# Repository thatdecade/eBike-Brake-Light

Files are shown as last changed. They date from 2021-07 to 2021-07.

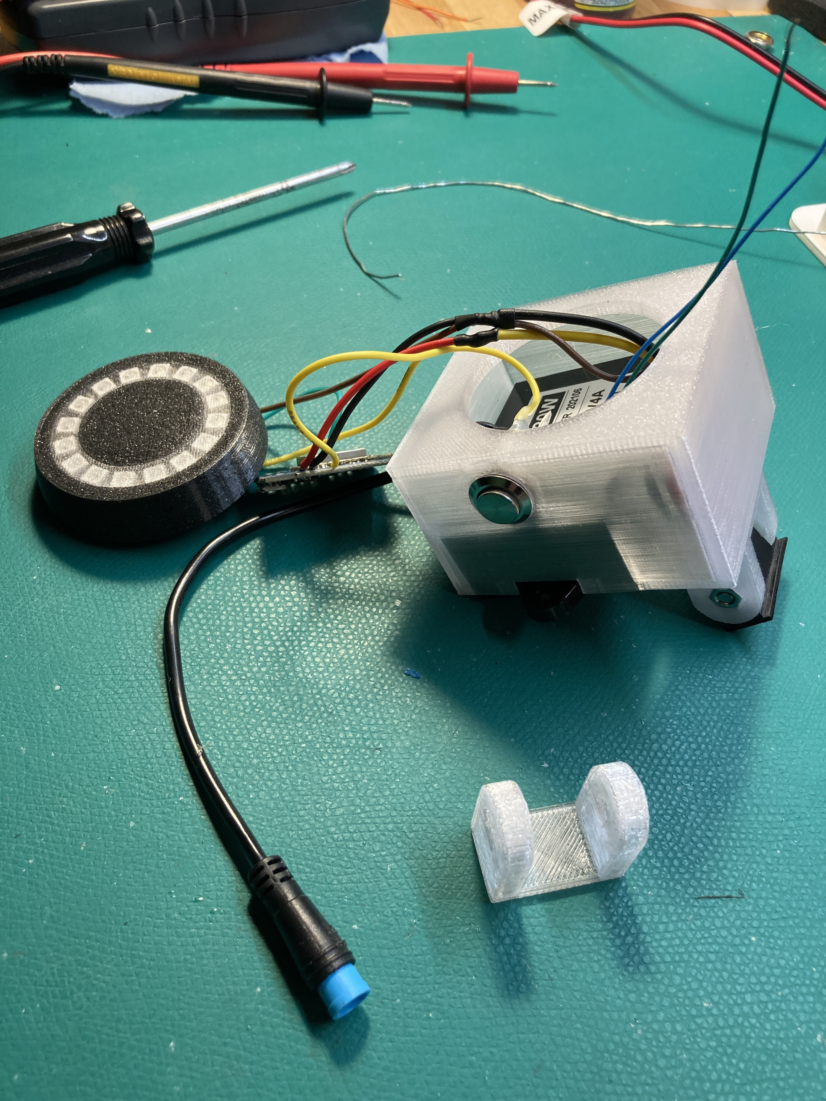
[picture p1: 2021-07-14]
photos/IMG_1149.jpg

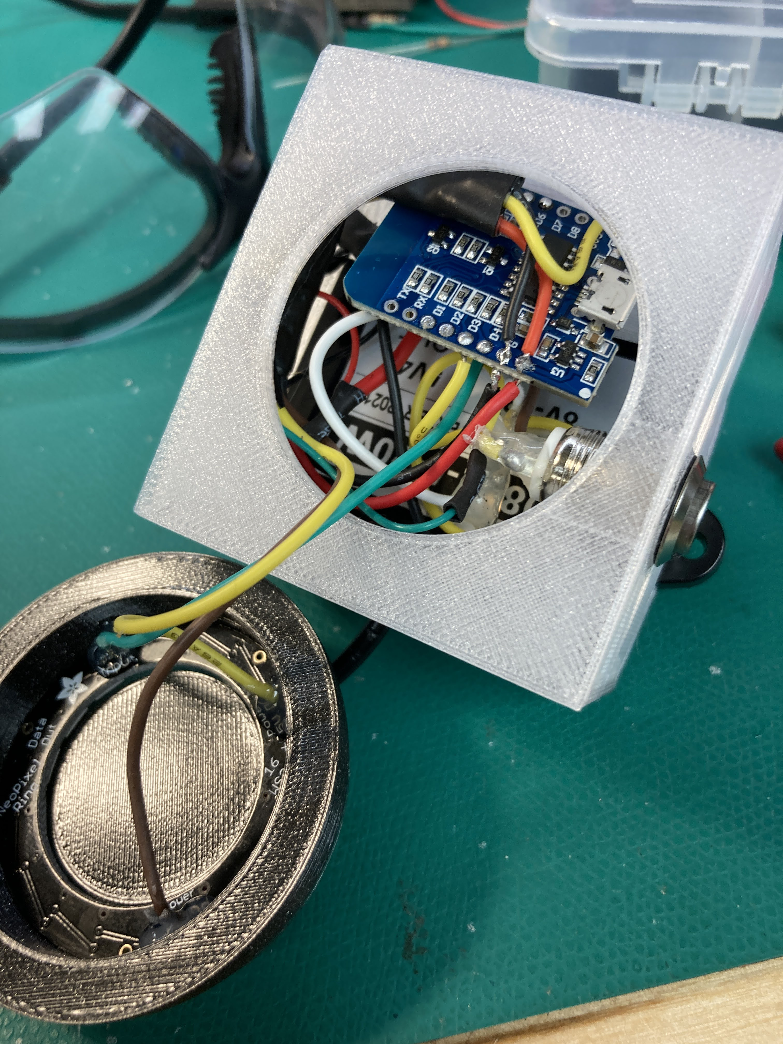
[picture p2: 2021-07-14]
photos/IMG_1154.jpg

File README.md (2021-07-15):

# eBike-Brake-Light
Neopixel Ring Based Brake Light

This is a brake light I made for my RadPower ebike.  Connects to the 4 pin wire harness from the motor controller.

The mount was modeled to replace my old Meilan light (https://amzn.to/3edWSh7) and re-use the same attachment bolt.  The openscad file is included, so you can change the mount to fit your project.



We are a participant in the Amazon Services LLC Associates Program, an affiliate advertising program designed to provide a means for us to earn fees by linking to Amazon.com and affiliated sites.

# Part List:

* Bafang 4 pin extension cable https://amzn.to/36BLSG1
* 8-72V to 5V 4A DCDC Converter https://amzn.to/3i4d8lV
* Wemos Mini dev board https://amzn.to/3xJ0e3q
* Adafruit neopixel Ring 16 https://amzn.to/3hDBBj0
* Pushbutton https://amzn.to/3egmDxg
* Resistors (5M / 10M) for voltage divider

# Wiring:

* 4 pin cable Red Wire -> DCDC +V Input
* 4 pin cable Black Wire -> DCDC GND Input
* 4 pin cable Green Wire -> +4.8V Voltage Divider
* 4 pin cable Blue Wire -> NO CONNECTION

* Wemos Pin 5V -> DCDC +V Output -> Neopixel V+
* Wemos Pin GND -> DCDC GND Output -> Neopixel GND -> Button GND

* Wemos Pin D3 -> Button
* Wemos Pin A0 -> 3.2V Brake Signal
* Wemos Pin D5 -> Neopixel Data In

# Cable Harness Wiring Notes:

The motor controller's 4 pin wire harness has two +52V and two grounds.  The voltages from the red and green wires are not meant to be combined, they do not have a common ground.  The red/black wire is supposed to power your 52V running lights, and the green/blue wire is supposed to power your 52V brake light.  I want all these signals running to a single circuit.

Here are some of the voltages I measured:

|Wire Pair|Lights Off|Lights On|Brake|Notes|
| --- | --- |  --- |  --- |  --- |
|Red / Black| 0| 52| 52| Correct ground|
|Green / Black| 4.8| 0| 4.8|Wrong ground|
|Blue / Black| 52| 52| 52|Wrong ground|
|Green / Blue| 0| 52| 0|Correct ground|
|Red / Blue| 52| 1.42| 1.55|Wrong ground|
|Red / Green| 4.8| 52| 52|Wrong ground|

**Correct ground**: These wires can sink current.
**Wrong ground**: Voltage drops to 0V if used for more than a few microamps.

There are a couple of ways to solve this.  
1. An optical isolator would be best.  Allowing the green/blue 52V brake signal to light up an LED, which then triggers a phototransistor to send a signal to our second 52V circuit.
2. Less good would be to try an read one circuit from the other using resistors and mixing the grounds.

I went with the second method.  The resistors are in the megaohm range, so less than 1uA is drawn from the green wires. The voltage does not drop and I can read it with an analog input set to detect a 0.2V threshold.

```

Green +4.8V ------- /\/\5M/\/\-+
                               |
                               +------ 3.2V to A0
                               |
Black GND   ------ /\/\10M/\/\-+

```

The wemos A0 pin has an additional voltage divider so the resulting signal is below 1V.  Measured 0.4V (idle) / 0.01V (brake)

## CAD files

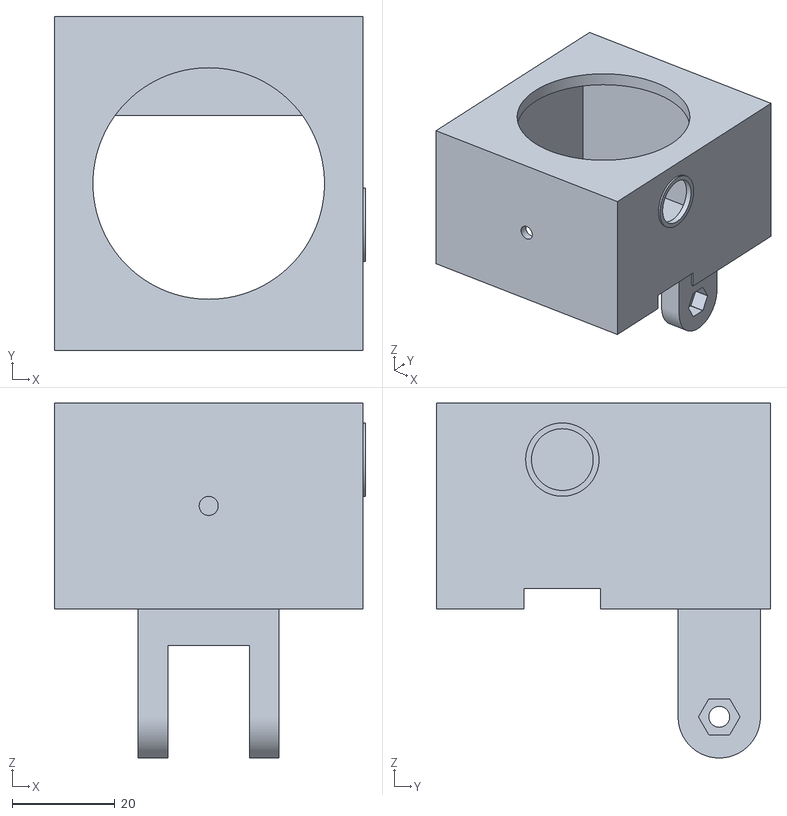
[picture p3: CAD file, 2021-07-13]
3D Model/tail light housing.stl
60.5 x 65.0 x 69.0

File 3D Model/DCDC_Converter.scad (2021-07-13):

wall_thickness = 2;

outer_dim_x = 58;
outer_dim_y = 40.1;
outer_dim_z = 22;

screwhole_offset_from_center = 65/2;
screwhole_diameter = 3.7;
screw_holder_radius = 4.64;
screw_holder_z = 4;
screw_holder_angle = 35;

module dcdc_converter()
{
    translate([-outer_dim_x/2,-outer_dim_y/2,0]) cube([outer_dim_x, outer_dim_y, outer_dim_z]);

    //screw_holder(screwhole_offset_from_center);
    translate([-screwhole_offset_from_center,0,0]) screw_holder();
    translate([screwhole_offset_from_center,0,0]) rotate([0,0,180]) screw_holder();
    
    wire_channel();
}

module wire_channel()
{
    wire_bend_x = outer_dim_x;
    wire_bend_y = 10;
    wire_bend_z = outer_dim_z - wall_thickness;
    wire_bend_z_offset = outer_dim_z-wire_bend_z;
    wire_bend_z_overhang = 10;
    
    //allow for wire bend radius
    translate([0,outer_dim_y/2+wire_bend_y/2,wire_bend_z_offset+(wire_bend_z+wire_bend_z_overhang)/2]) cube([wire_bend_x, wire_bend_y, wire_bend_z + wire_bend_z_overhang], center=true);
}

module screw_holder()
{
    difference()
    {
        union()
        {
            //flange
            translate([0,0,0]) cylinder(h=screw_holder_z, r=screw_holder_radius, $fn=25);
             
            //angled flange edge
            translate([0,0,0]) 
            rotate([0,0,screw_holder_angle]) cube([screw_holder_radius*2,screw_holder_radius,screw_holder_z]);
            translate([0,0,0]) rotate([0,0,-screw_holder_angle]) translate([0,-screw_holder_radius,0]) cube([screw_holder_radius*2,screw_holder_radius,screw_holder_z]);
        }
        
        //hole
        translate([0,0,-0.1]) cylinder(h=screw_holder_z+0.2, d=screwhole_diameter, $fn=25);
    }
}

dcdc_converter();

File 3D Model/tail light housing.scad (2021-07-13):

use <DCDC_Converter.scad>;
use <ESP8266Models.scad>;

want_lens = 0;
want_ring_top = 0;
want_print_ready_rotate = 0;

z_height_adj = 2;

$fn=100;

wall_thickness = 2;
water_tight_overhang_y = 2;

watertight_y_offset = 9 + 6; //extra clearance

neopixel_outerRadius = 45 / 2;
neopixel_innerRadius = 31.37 / 2 - 0.2;
neopixel_height = 3.26;

outer_dim_x = 60;
outer_dim_y = 45 + wall_thickness*2;
outer_dim_z = 38 + z_height_adj;

inner_dim_x = 58;
inner_dim_y = 45;
inner_dim_z = outer_dim_z - neopixel_height;

wire_bend_y = 16; //dcdc wire channel
dcdc_outer_dim_z = 22;

sphere_z = 50;
sphere_d = outer_dim_x - 2;

diffuser_lens_diameter = sphere_d-5;
diffuser_lens_thickness = 0.4;

switch_z_offset = 29;

cable_diameter = 3.5 + 0.2;

/* ***************************** */

if (want_print_ready_rotate)    {rotate([-180,0,0]) main_body();} else {main_body();} 

/* ***************************** */

module main_body()
{
    difference()
    {
        union()
        {
            outer_box();
        }
        
        union()
        {
            inner_cavity();
            translate([0,0,-0.01]) dcdc_converter();
            translate([0,wire_bend_y/2,diffuser_lens_thickness+sphere_z/2]) neopixel_ring();
            /* for alignment only */ //translate([0,0,26]) WemosD1M(pins=0);
        }
    }
    water_tight_edge();

    //transparent lid.
    if (want_lens) color("red") translate([0,wire_bend_y/2,sphere_z]) cylinder(h=diffuser_lens_thickness, d=diffuser_lens_diameter);

    screw_mounts();
}
/* ***************************** */

screw_holder_width = 5.8;
holder_diameter = 16;
holder_outreach_z = 21;

module screw_mount(x_position, y_offset)
{
    screw_hole_diameter = 4.05;
    
    
    difference()
    {
        union()
        {
            translate([x_position,y_offset,-holder_outreach_z]) rotate([0,90,0])
            cylinder(d=holder_diameter, h=screw_holder_width);
            
            translate([x_position,y_offset-holder_diameter/2,-holder_outreach_z])
            cube([screw_holder_width,holder_diameter,holder_outreach_z]);
        }
    
    
        translate([x_position-0.1,y_offset,-holder_outreach_z]) rotate([0,90,0])
        cylinder(d=screw_hole_diameter, h=screw_holder_width+0.2);
    }
}

module draw_nut()
{
    nut_outer_size = 6.82 + 0.2;
    nut_edge_size = 4 + 0.02;
    nut_thickness = 2.94 + 1;
    nut_sides = 6;
    
    translate([nut_thickness,0,0])
    for ( i = [0 : nut_sides] ){
        rotate([i*(360/nut_sides),0,0]) cube([nut_edge_size,nut_thickness,nut_outer_size], center=true);
    }
}

module screw_mounts()
{
    holder_total_width_outside = 27.4;
    holder_total_width_inside = holder_total_width_outside - screw_holder_width*2;
    strength_block_z = 7.13;
    
    y_offset = outer_dim_y/2+wire_bend_y/2-wall_thickness;
    
    //screw holders
    //nut side
    nut_side_x_pos = holder_total_width_inside/2;
    difference()
    {
        screw_mount(nut_side_x_pos, y_offset);
        translate([nut_side_x_pos-0.1,y_offset,-holder_outreach_z]) draw_nut();
        
    }
    
    //screw side
    screw_side_x_pos = -holder_total_width_inside/2-screw_holder_width;
    screw_head_clearance_diameter = 11.3;
    difference()
    {
        screw_mount(screw_side_x_pos, y_offset);
        translate([screw_side_x_pos-0.1,y_offset,-holder_outreach_z]) rotate([0,90,0]) cylinder(d=screw_head_clearance_diameter, h=3.94);
    }
    
    //strength block
    translate([0,y_offset,-strength_block_z/2])
    cube([holder_total_width_outside,holder_diameter,strength_block_z], center=true);
}

module water_tight_edge()
{
    new_y = outer_dim_y - inner_dim_y;
    
    //top
    translate([0,outer_dim_y/2-new_y/2+watertight_y_offset/2,wall_thickness/2]) cube([outer_dim_x,outer_dim_y/2+wire_bend_y/2-watertight_y_offset,wall_thickness], center=true);
    
    //bottom
    translate([0,-outer_dim_y/2+new_y/2,wall_thickness/2]) cube([outer_dim_x,new_y,wall_thickness], center=true);
}


module outer_box()
{
    outer_x = outer_dim_x;
    outer_y = outer_dim_y;
    outer_z = outer_dim_z;
    
    //outer edges
    translate([0,wire_bend_y/2,outer_z/2]) cube([outer_x,outer_y+wire_bend_y,outer_z], center=true); 
    
    //rounded top
    if (want_ring_top) intersection()
    {
        translate([0,wire_bend_y/2,outer_z])sphere(d=sphere_d);
        translate([0,wire_bend_y/2,sphere_z/2]) cube([outer_x,outer_y+wire_bend_y,sphere_z], center=true); 
    }
    
    
    draw_switch_outline();
}

module inner_cavity()
{
    inner_wire_bend_y = wire_bend_y - wall_thickness;
    
    //cube cutout
    translate([-inner_dim_x/2,-inner_dim_y/2,-0.01]) cube([inner_dim_x, inner_dim_y + inner_wire_bend_y, inner_dim_z]);
    
    //ring wall thickness
    translate([0,wire_bend_y/2,diffuser_lens_thickness+sphere_z/2]) translate([0,0,-13]) cylinder(r=neopixel_innerRadius + 0.1,h=outer_dim_z-wall_thickness);
    
    draw_switch_holes();
    draw_cable_hole();
}

module neopixel_ring()
{
    $fn = 120;

    centerRadius = (neopixel_outerRadius + neopixel_innerRadius) / 2;
    ringThickness = (neopixel_outerRadius - neopixel_innerRadius);

    difference() 
    {
        cylinder(r=neopixel_outerRadius,h=outer_dim_z);
        translate([0,0,-13])
        cylinder(r=neopixel_innerRadius,h=outer_dim_z+0.02);
    }

}

module draw_cable_hole()
{
    cutout_height = wall_thickness+wire_bend_y;
    
    translate([0,-outer_dim_y/2+cutout_height-0.1,outer_dim_z/2]) rotate([90,0,0]) cylinder(d=cable_diameter,h=cutout_height);
}

/* ***************************** */

switch_hole_diameter = 12;
shell_thickness = wall_thickness;
switch_outline_pad = 2.25;
ring_stick_out = 0.5;

hole_depth = shell_thickness + ring_stick_out;

module draw_switch_cyl(diameter, height, offset)
{
    //switch_hole_diameter
    translate([offset,0,switch_z_offset]) rotate([90,0,90]) cylinder(h=height, d=diameter);
}

module draw_switch_outline()
{
    draw_switch_cyl(switch_hole_diameter+switch_outline_pad, ring_stick_out, outer_dim_x/2);
}

module draw_switch_holes()
{
    translate([0.01,0,0]) draw_switch_cyl(switch_hole_diameter, ring_stick_out+shell_thickness, outer_dim_x/2-shell_thickness);
    
    translate([-1,0,0]) draw_switch_cyl(switch_hole_diameter+7, 10, outer_dim_x/2-10);
}

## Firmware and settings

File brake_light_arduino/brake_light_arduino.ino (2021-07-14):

#include <ESP8266WiFi.h>
#include <ESP8266mDNS.h>
#include <WiFiUdp.h>
#include <ArduinoOTA.h>
#include <Adafruit_NeoPixel.h>

const char* ssid = "";
const char* password = "";

#define SLOW_TIMING 400
#define FAST_TIMING 100

#define BUTTON_HOLD_DELAY_IN_MILLIS_UNTIL_HELD_ACTION     2000 // 2 seconds

#define BUTTON_PIN D3
#define BRAKE_PIN  D6
 
#define NEOPIN D5
// How many NeoPixels are attached to the Arduino?
#define NUMPIXELS 16
 
Adafruit_NeoPixel pixels = Adafruit_NeoPixel(NUMPIXELS, NEOPIN);

/* ***************** */
//mode info

enum animations_e
{
  /* order of animations list */
  CYLON_BOUNCE = 0,
  
  FLASHING_SLOW_RED,
  FLASHING_FAST_RED,
  SOLID_RED,
  
  FLASHING_SLOW_GREEN,
  FLASHING_FAST_GREEN,
  SOLID_GREEN,
  
  OFF,
  
  /* keep at end of list */
  NUMBER_OF_ANIMATIONS,
  
  GRUNT_BDAY_PARTY, //secret
};

byte animation_mode = 0;

bool brake_flag = false;

bool wifi_connected = false;

/* ***************** */
//button routines
typedef enum switch_status { PROCESSED, NOT_PROCESSED, };
typedef enum switch_state  { IS_NOT_PRESSED, IS_PRESSED, WAS_RELEASED, IS_HELD, };
typedef enum input_type    { ACTIVE_HIGH, ACTIVE_LOW, };

enum button_link
{
  /* order of button_info list */
  PUSHBUTTON = 0,
  //BRAKE_SIGNAL, // process in real time
  /* keep at end of list */
  NUMBER_OF_BUTTONS,
};

typedef struct
{
  byte          pin;
  input_type    in_type;
  switch_state  state;
  switch_status status;
  long          last_interaction_timestamp;
  byte          last_button_read;
  byte          current_button_read;
} button_struct;

button_struct button_info[NUMBER_OF_BUTTONS] =
{
  { /* button_info[PUSHBUTTON] */
    /* pin       = */ BUTTON_PIN,
    /* in_type   = */ ACTIVE_LOW,
    /* state     = */ IS_NOT_PRESSED,
    /* status    = */ NOT_PROCESSED,
    /* timestamp = */ 0,
    /* last      = */ false,
    /* current   = */ false,
  },
};

/* ***************** */

void setup() 
{
  //setup output to serial monitor
  Serial.begin(115200);
  
  // initialize the button pins as an input:
  for (byte i = 0; i < NUMBER_OF_BUTTONS; i++)
  {
    if (button_info[i].in_type == ACTIVE_HIGH)
    {
      pinMode(button_info[i].pin, INPUT); //special pin, Active = 3.3V
    }
    else
    {
      pinMode(button_info[i].pin, INPUT_PULLUP);
    }
  }

  pinMode(BRAKE_PIN, INPUT); //no pullup, is active high

  pixels.begin();
  set_idle_brightness();
  
  Serial.println(F("Bike Light v1.0"));

}

void loop() 
{
  poll_brake_signal_for_brightness();
  poll_input_signals();
  process_button_presses();
  process_animation();
  //TBD, brake should override the animation, not directly change the mode
}

void poll_brake_signal_for_brightness()
{
  static bool last_flag = false;
  int sensorValue = analogRead(A0);
  float voltage = sensorValue * (3.2 / 1023.0);

  //Serial.print("Brake: ");
  //Serial.println(voltage);

  if (voltage < 0.1f) //check for active low signal (not strong enough for digital input)
  {
    brake_flag = true;
  }
  else
  {
    brake_flag = false;
  }

  if(brake_flag != last_flag) //change brightness only on state changes
  {
    last_flag = brake_flag;
    if(brake_flag) set_high_brightness();
    else set_idle_brightness();
  }
}

void start_wifi()
{
  uint32_t timeout = millis();

  WiFi.mode(WIFI_STA);
  WiFi.begin(ssid, password);
  
  while ( ( (timeout + 5000) > millis() ) && 
          ( WiFi.waitForConnectResult() != WL_CONNECTED) );
  
  if(WiFi.waitForConnectResult() != WL_CONNECTED)
  {
    wifi_connected = false;
    Serial.println("Connection Failed! Rebooting...");
    delay(1000);
    ESP.restart();
  }
  else
  {
    wifi_connected = true;
  }

  if(wifi_connected)
  {
    ArduinoOTA.onStart([]() {
      Serial.println("Start");
    });
    ArduinoOTA.onEnd([]() {
      Serial.println("\nEnd");
    });
    ArduinoOTA.onProgress([](unsigned int progress, unsigned int total) {
      Serial.printf("Progress: %u%%\r", (progress / (total / 100)));
    });
    ArduinoOTA.onError([](ota_error_t error) {
      Serial.printf("Error[%u]: ", error);
      if (error == OTA_AUTH_ERROR) Serial.println("Auth Failed");
      else if (error == OTA_BEGIN_ERROR) Serial.println("Begin Failed");
      else if (error == OTA_CONNECT_ERROR) Serial.println("Connect Failed");
      else if (error == OTA_RECEIVE_ERROR) Serial.println("Receive Failed");
      else if (error == OTA_END_ERROR) Serial.println("End Failed");
    });
    ArduinoOTA.begin();
    Serial.println("Ready");
    Serial.print("IP address: ");
    Serial.println(WiFi.localIP());
  }
  else
  {
    Serial.println("Wifi Not Connected");
  }
}

//--------------------------------------
//          Mode Subroutines           |
//--------------------------------------

void next_animation()
{
  if ((animation_mode + 1) < NUMBER_OF_ANIMATIONS)
  {
    animation_mode++;
  }
  else
  {
    animation_mode = 0;
  }
  
  Serial.print("Mode: ");
  Serial.println(animation_mode);
}

void secret_animation()
{
  //hold to enter / exit
  if(animation_mode != GRUNT_BDAY_PARTY)
  {
    start_wifi();
    animation_mode = GRUNT_BDAY_PARTY;
  }
  else
  {
    animation_mode = 0; 
  }
  
  Serial.print("Mode: ");
  Serial.println(animation_mode);
}

//--------------------------------------
//        Neopixel Subroutines         |
//--------------------------------------

void process_animation()
{
  if (brake_flag) //BRAKE !!
  {
    switch (animation_mode)
    {
      case FLASHING_SLOW_RED:
      case FLASHING_FAST_RED:
      case SOLID_RED:
      case CYLON_BOUNCE:
      case OFF:
        fill_ring(pixels.Color(255,0,0)); //red
        break;
        
      case FLASHING_SLOW_GREEN:
      case FLASHING_FAST_GREEN:
      case SOLID_GREEN:
        fill_ring(pixels.Color(0,255,0)); //red
        break;
    
      case GRUNT_BDAY_PARTY:
        rainbow(1);
        if(wifi_connected)
        {
          ArduinoOTA.handle();
        }
        break;
      default:
        break;
    }
  }
  else //NO BRAKE, NORMAL ANIMATION
  {
    switch (animation_mode)
    {
      case FLASHING_SLOW_RED:
        flash_animation(SLOW_TIMING, pixels.Color(255,0,0));
        break;
      case FLASHING_FAST_RED:
        flash_animation(FAST_TIMING, pixels.Color(255,0,0));
        break;
      case SOLID_RED:
        fill_ring(pixels.Color(255,0,0)); //red
        break;
        
      case FLASHING_SLOW_GREEN:
        flash_animation(SLOW_TIMING, pixels.Color(0,255,0));
        break;
      case FLASHING_FAST_GREEN:
        flash_animation(FAST_TIMING, pixels.Color(0,255,0));
        break;
      case SOLID_GREEN:
        fill_ring(pixels.Color(0,255,0)); //red
        break;

      case CYLON_BOUNCE:
        CylonBounce(0xff, 0, 0, 4, 10, 50);
        break;

      case OFF:
        fill_ring(pixels.Color(0,0,0)); //black / off
        break;
      case GRUNT_BDAY_PARTY:
        rainbow(1);
        if(wifi_connected)
        {
          ArduinoOTA.handle();
        }
        break;
      default:
        Serial.print("Unknown Mode: ");
        Serial.println(animation_mode);
        break;
    }
  }
}

// Rainbow cycle along whole strip. Pass delay time (in ms) between frames.
void rainbow(int wait) 
{
  static long firstPixelHue = 0;
  static int i = 0;
  static uint32_t last_update = 0;

  if (last_update + wait < millis())
  {
    last_update = millis();
    
    //for(long firstPixelHue = 0; firstPixelHue < 3*65536; firstPixelHue += 256) 
    {
      //for(int i=0; i<pixels.numPixels(); i++) 
      {
        int pixelHue = firstPixelHue + (i * 65536L / pixels.numPixels());
        pixels.setPixelColor(i, pixels.gamma32(pixels.ColorHSV(pixelHue)));
        
        if (i<pixels.numPixels())
        {
          i++;
        }
        else
        {
          i = 0;
        }
      }
      pixels.show();
      
      if (firstPixelHue < 3*65536)
      {
        firstPixelHue += 256;
      }
      else
      {
        firstPixelHue = 0;
      }
    }
  }
}

void flash_animation(uint32_t time_delay, uint32_t color)
{
  static uint32_t last_update = 0;
  static bool flash_state = LOW;

  if (last_update + time_delay < millis())
  {
    last_update = millis();

    flash_state = !flash_state;

    if (flash_state == LOW)
    {
      fill_ring(pixels.Color(0,0,0)); //black / off
    }
    else
    {
      fill_ring(color);
    }
  }
}

void set_high_brightness()
{
 pixels.setBrightness(255);
}

void set_idle_brightness()
{
 pixels.setBrightness(64);
}

void fill_ring(uint32_t color)
{
 for(int i=0;i<NUMPIXELS;i++)
 {
   pixels.setPixelColor(i, color);
 }
   pixels.show();
}


//--------------------------------------
//            Imported Code            |
//--------------------------------------
//https://www.tweaking4all.com/hardware/arduino/adruino-led-strip-effects/#LEDStripEffectCylon
// Modified to run without delays

void CylonBounce(byte red, byte green, byte blue, int EyeSize, int SpeedDelay, int ReturnDelay)
{
  static bool animation_direction = true;
  static int i = 0;
  static uint32_t last_update = 0;

  if (last_update + SpeedDelay < millis())
  {
    last_update = millis();
    
    if (animation_direction)
    {
      setAll(0,0,0);
      setPixel(i, red/10, green/10, blue/10);
      for(int j = 1; j <= EyeSize; j++) {
        setPixel(i+j, red, green, blue);
      }
      setPixel(i+EyeSize+1, red/10, green/10, blue/10);
      pixels.show();
      
      if(i < pixels.numPixels()-EyeSize-2)
      {
        i++;
      }
      else
      {
        animation_direction = false;
        i = pixels.numPixels()-EyeSize-2;
        delay(ReturnDelay);
      }
    }
    else
    {
      setAll(0,0,0);
      setPixel(i, red/10, green/10, blue/10);
      for(int j = 1; j <= EyeSize; j++) {
        setPixel(i+j, red, green, blue);
      }
      setPixel(i+EyeSize+1, red/10, green/10, blue/10);
      pixels.show();
      
      if(i > 0)
      {
        i--;
      }
      else
      {
        animation_direction = true;
        i = 0;
        delay(ReturnDelay);
      }
    }
  }
}

void setPixel(int Pixel, byte red, byte green, byte blue) 
{
   pixels.setPixelColor(Pixel, pixels.Color(red, green, blue));
}

void setAll(byte red, byte green, byte blue) 
{
  for(int i = 0; i < pixels.numPixels(); i++ ) 
  {
    setPixel(i, red, green, blue);
  }
  pixels.show();
}

//--------------------------------------
//          Button Subroutines         |
//--------------------------------------

void process_button_presses()
{
  for (byte i = 0; i < NUMBER_OF_BUTTONS; i++)
  {
    if (button_info[i].state == WAS_RELEASED)
    {
      //CLICKED ACTION

      //Note: action taken on WAS_RELEASED instead of IS_PRESSED to prevent extra clicks during button holds

      button_info[i].last_interaction_timestamp = millis();

      if (button_info[i].status == NOT_PROCESSED)
      {
        //one action per press / hold for all buttons
        for (byte j = 0; j < NUMBER_OF_BUTTONS; j++)
        {
          button_info[j].status = PROCESSED;
        }

        //button was clicked
        switch (i)
        {
          case PUSHBUTTON:
            next_animation();
            break;
          default:
            break;
        }
      }
    }
    else if ( ( button_info[i].state == IS_HELD ) &&
              ( button_info[i].last_interaction_timestamp + BUTTON_HOLD_DELAY_IN_MILLIS_UNTIL_HELD_ACTION < millis() ) )
    {
      //HELD ACTION

      button_info[i].last_interaction_timestamp = millis();

      if (button_info[i].status == NOT_PROCESSED)
      {
        //one action per press / hold for all buttons
        for (byte j = 0; j < NUMBER_OF_BUTTONS; j++)
        {
          button_info[j].status = PROCESSED;
        } //TBD, move this to a routine

        //button was held
        switch (i)
        {
          case PUSHBUTTON:
            secret_animation();
            break;
          default:
            break;
        }
      }
    }
    else if (button_info[i].state == IS_NOT_PRESSED)
    {
      //reset timers
      button_info[i].last_interaction_timestamp = millis();
      button_info[i].status = NOT_PROCESSED;
    }

  }// end for loop
}

void poll_input_signals()
{
  for (byte i = 0; i < NUMBER_OF_BUTTONS; i++)
  {
    if ( button_info[i].in_type == ACTIVE_HIGH )
    {
      /* read digital active high beam signal */
      button_info[i].current_button_read = digitalRead(button_info[i].pin);
    }
    else // button_info[i].in_type == ACTIVE_LOW
    {
      /* read digital active low button signal */
      button_info[i].current_button_read = !digitalRead(button_info[i].pin);
    }

    if (!button_info[i].last_button_read && button_info[i].current_button_read)
    {
      //button was just pressed
      button_info[i].state = IS_PRESSED;
    }
    else if  (button_info[i].last_button_read && button_info[i].current_button_read)
    {
      button_info[i].state = IS_HELD;
    }
    else if (button_info[i].last_button_read && !button_info[i].current_button_read)
    {
      //button was just released
      button_info[i].state = WAS_RELEASED;
    }
    else
    {
      button_info[i].state = IS_NOT_PRESSED;
    }

    button_info[i].last_button_read = button_info[i].current_button_read;
  }
}

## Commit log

2021-07-13 Initial check in
    [DCDC_Converter.scad, tail light housing.scad, tail light housing.stl]
2021-07-13 Added mounting link
